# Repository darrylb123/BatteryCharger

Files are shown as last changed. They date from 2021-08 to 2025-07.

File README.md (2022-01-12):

# BatteryCharger
Multiplexed Battery Charger for maintaining up to 7 batteries from one charger, an 8th battery can be connected and charged but not maintained.

Based on the ESP12F\_Relay\_X8\_V1.1 integrated ESP8266 8 relay board.
A connected charger cycles through each battery in turn. The analog input monitors the battery terminal voltage of the battery. 

The charger is disconnected to measure the actual battery terminal volts by the No 8 relay therefore each module can manage 7 batteries. 

The board operates as an AP with captive portal or connects to a local network. Connecting to the AP with a mobile phone displays the normal captive portal login page, in this case it simply displays the battery status.
Use the Expressif Android app to connect the wifi the local network.

Electricals drawings by Qelectrotech.

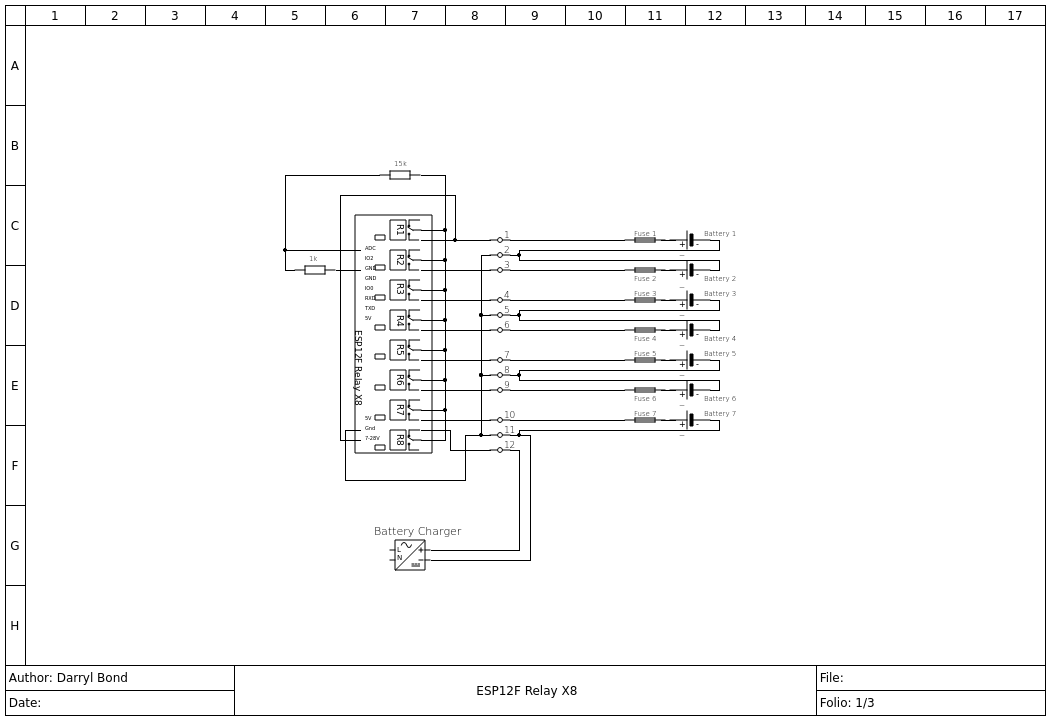
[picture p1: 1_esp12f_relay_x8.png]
7 Battery Wiring Diagram
 

## Construction
	- Connect the 1k resistor  between the ADC and GND and the 15k resistor between ADC and one of the COM terminals. (see Photograph)
	- Connect the 7-28V terminal to the NO8 relay
	- Connect the GND to the battery ground on the external terminal strip.
	- Follow the schematic to jumper between the module terminal strip and the external terminal strip.

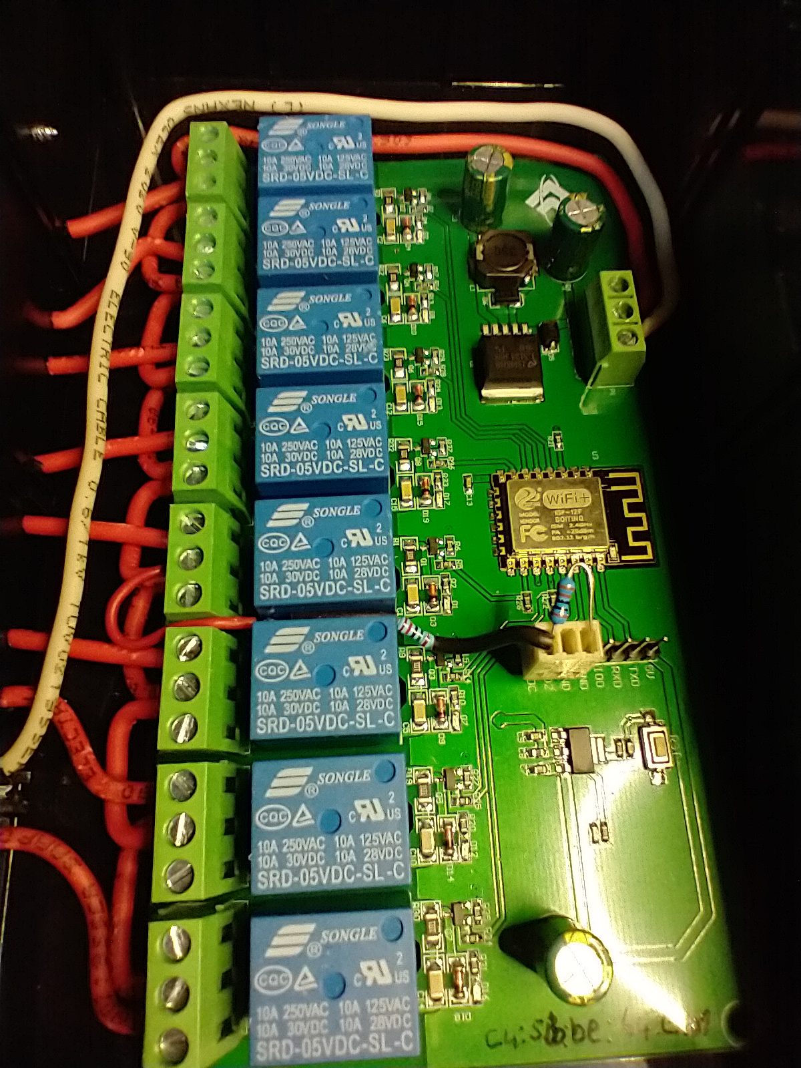
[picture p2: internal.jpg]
Relay module wiring

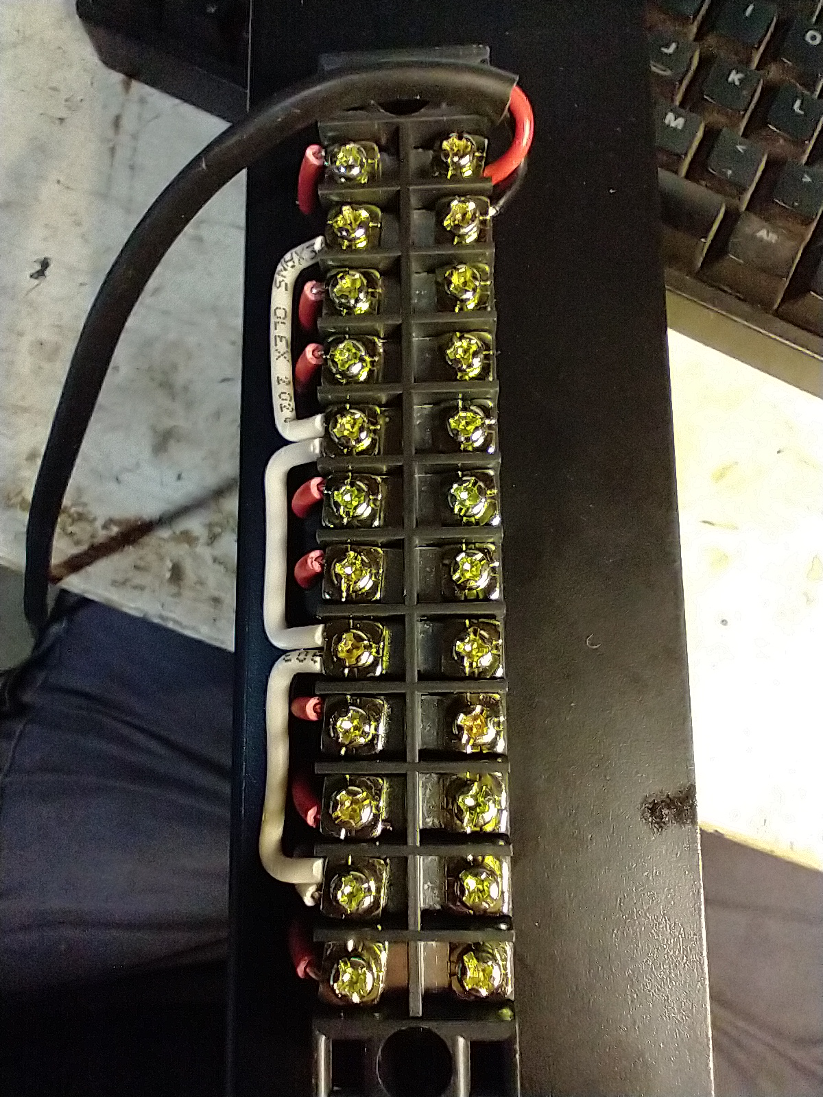
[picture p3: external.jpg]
External strip wiring


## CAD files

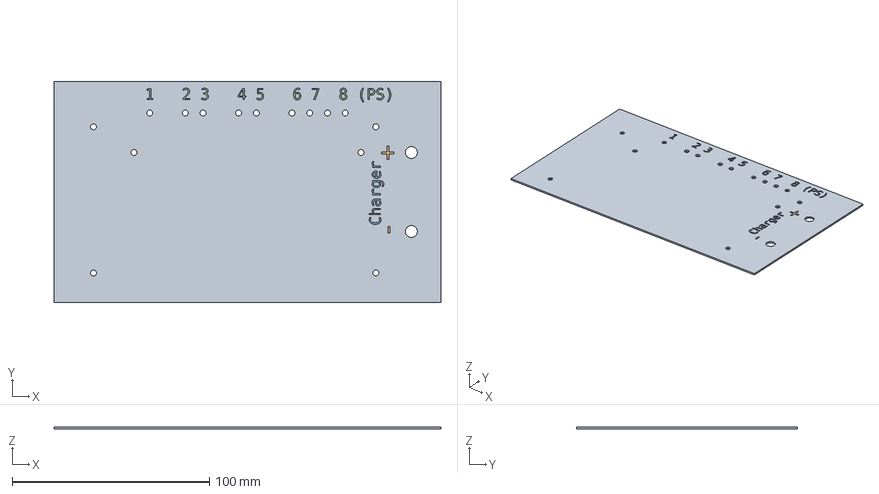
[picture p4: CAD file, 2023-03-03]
BatteryChargerLid.FCStd
196.0 x 112.0 x 1.00 mm
+-String
ChargerString
ShapeString002

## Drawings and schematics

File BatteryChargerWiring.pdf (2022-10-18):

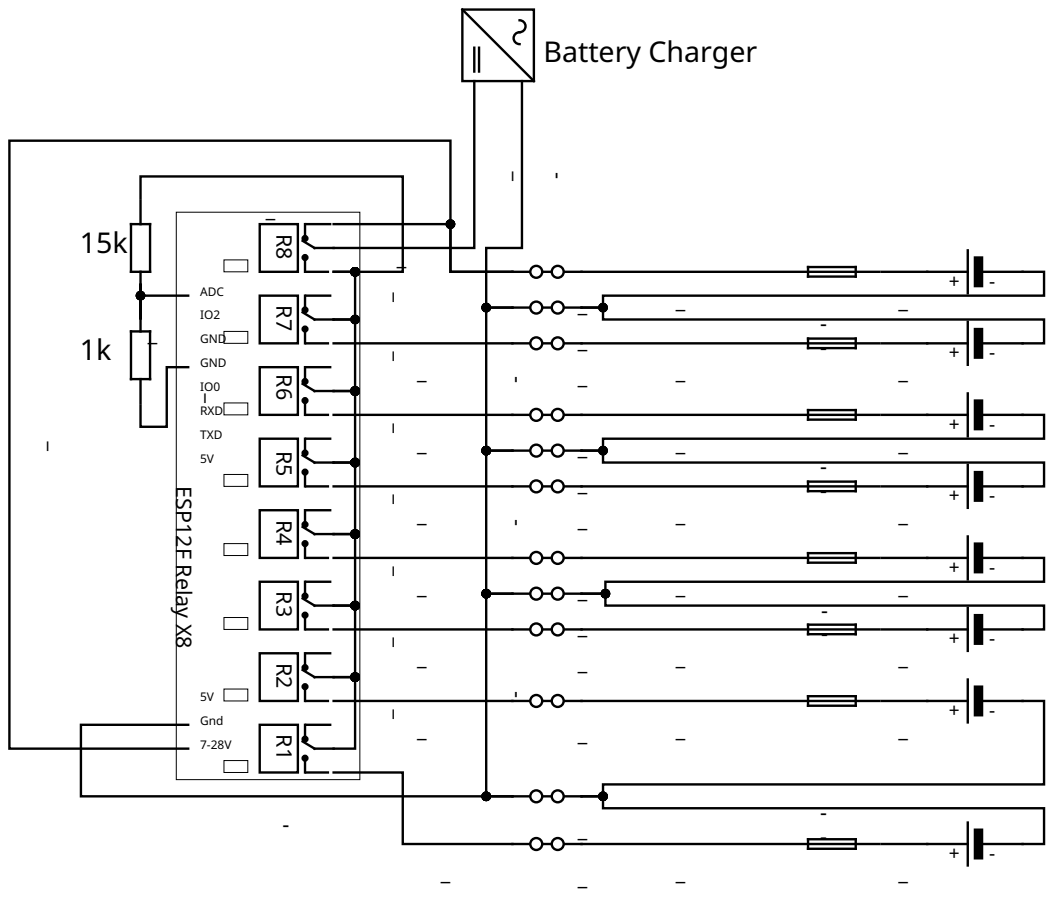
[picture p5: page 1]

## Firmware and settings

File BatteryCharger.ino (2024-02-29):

/* Battery Charger Multiplexer using ESP8266 or ESP32*/
/*
Copyright (C) 2021  Darryl Bond
This program is free software; you can redistribute it and/or modify
it under the terms of the GNU General Public License as published by
the Free Software Foundation; either version 2 of the License, or
(at your option) any later version.
This program is distributed in the hope that it will be useful,
but WITHOUT ANY WARRANTY; without even the implied warranty of
MERCHANTABILITY or FITNESS FOR A PARTICULAR PURPOSE.  See the
GNU General Public License for more details.
You should have received a copy of the GNU General Public License along
with this program; if not, write to the Free Software Foundation, Inc.,
51 Franklin Street, Fifth Floor, Boston, MA 02110-1301 USA.
*/
#define STATION 1
// #define SOFTAP 1
#define VER2 1
#define DEBUG 0
#define NEEDMQTT 1
#include <stdio.h>
#include <Ticker.h>

#if defined(VER2)
#define ENERG LOW
#define DEENERG HIGH
#else
#define ENERG HIGH
#define DEENERG LOW
#endif


#include "DNSServer.h"                  // Patched lib
// Capture DNS requests on port 53 in SoftAP Mode
IPAddress         apIP(10, 10, 10, 1);    // Private network for server
DNSServer         dnsServer;              // Create the DNS object



#include <ESP8266WiFi.h>
#include <ESP8266WiFiType.h>

const int RELAYS = 7;

struct Config {
  String mqttBroker;
  int mqttPort;
  String mqttUser;
  String mqttPasswd;
  String mqttTopic;
  float calConst;
  String labelTXT[RELAYS];
};

Config config;    // <- global configuration object

// An array of charging time indexed by the measured voltage. Allows a flat battery to be charged longer and a fully charged battery to be charged for a short time
// Volts                     0, 1,  2,  3,  4,  5,  6,  7,  8,    9,    10,   11,   12, 13, 14, 15, 16
const int CHARGEMINUTES[] = {1, 1,  1,  1,  60,  30, 10, 1, 240,  240,  240,  100,  10, 1,  1,  1,  1};
const float fullyCharged[] = {6.2,11.9};
const byte        DNS_PORT = 53;
String inputString;
int stringComplete;
int needDNS;

Ticker minutes;








#if defined(VER2) 
const int gpioPin[] = { 16, 14, 12, 13, 15, 0, 4 };
const int chargeEnable =  5 ;
const int bankPin[] = { 3, 3, 3, 3, 3, 3, 3 }; // Relay bank enable pin
const float CALIBRATION = 0.0157521; //15k/1k ohm resistors. Analog in is 0-1V (12/782 measured)
#else
const int gpioPin[] = { 16, 5, 4, 14 ,12, 13, 0};
const int chargeEnable = 2;
// const int gpioPin[] = { 16, 5, 4, 0, 2, 14, 12 };
// const int chargeEnable = 13;
const int bankPin[] = { 15, 15, 15, 15, 15, 15, 15 }; // Relay bank enable pin
const float CALIBRATION = 0.014273256; // 8.2/2.2 ohm resistor divider (3.313 / .694V = 234 of 1024 )
#endif

const int sensorPin = A0;





const int SCAN = 1000; // Delay in ms between each battery when scanning 
const int TESTCYCLE = 15; // Cycle time for testing batteries
char sapString[30]; // SSID and mqtt name unique by reading chip ID
float batVolts[RELAYS];
int batteryCharged[RELAYS];
int batteryConnected[RELAYS];
int allCharged = 0;
int currentCharger = 0 ;
int sensorValue = 0;
int firstBoot = 1;
int lastMinutes, lastHour, lastDay;
int runMinutes = 0;
int runHours = 0;
int runDays = 0;
char *responseHTML;
int forceCharge = 0;
int forceScan = 0;



void setup() {
  Serial.begin(115200);
  // Start Minute Ticker
  // Ticker is where all the action happens
  minutes.attach(60, eachMinute);

  wifiStartup();
  configSetup();
  initialiseWebUI();
  

  
  pinMode(chargeEnable, INPUT);
  Serial.print("chargeEnable Pin reads: ");
  Serial.println(digitalRead(chargeEnable));
  // Set direction of IO
  pinMode(chargeEnable, OUTPUT);
  for (int i = 0; i < RELAYS; i++) {
    pinMode(gpioPin[i], OUTPUT);
    pinMode(bankPin[i], OUTPUT);
    digitalWrite(gpioPin[i], ENERG);
    digitalWrite(bankPin[i], DEENERG); // The bank pin supplies 3.3V for the optocouplers supply. DEENERG disables the particular bank
  }
  currentCharger = 0;
  forceCharge = 0;
  forceScan = 0;
  scanAll(); // Scan all Batteries on boot
  batteriesCharged(); // See if they are allCharged
  
 
  if (!allCharged) 
    pickBattery(currentCharger); //Start with the first battery
  lastMinutes = runMinutes;
  lastDay = runDays;
  firstBoot = 1;
  
  delay(1000);
}


// Function Runs from the minute ticker
// Does all the work with deciding when to change relays
void eachMinute (){
  // Routine runs every minute
  logbat();
  runMinutes++;
  if (runMinutes < lastMinutes){
    lastMinutes = runMinutes;
    lastDay = runDays;
  }
  if ( ! (runMinutes % TESTCYCLE) ) {
    runHours++;
  }
  if ( ! (runMinutes % 1440) ) {
    runDays++;
  }
  // Check if the charge time on current has expired and increment battery number
  // See if we have rolled over, delayed enough or current battery has < 1.2V
  // if all batteries are charged, pickBattery will set the lastDay 1 in front so that it waits until then to attempt charging again
  if (runMinutes >= (lastMinutes + CHARGEMINUTES[(int)batVolts[currentCharger]]) ) {
    lastMinutes = runMinutes;
    lastDay = runDays;
    currentCharger++;
  }
  
  if (allCharged)
    currentCharger = 0;

  if (currentCharger >= RELAYS ) { // At the end of a cycle check all the batteries to see if any need charging again
    currentCharger = 0;
    // Reset force Charge flag
    forceCharge = 0;
    scanAll(); 
  }
  // Check if all batteries are charged. pickBattery wont charge any if all charged
  pickBattery(currentCharger);
}

void scanAll(){
  int j;
  // scan all the batteries for voltage
  // Disable the charger to read actual battery volts
  Serial.println("Scanning");
  // Initialise all pins to off
  
  // Set all Charged to off to allow reading voltages
  allCharged = 0;
  currentCharger = 0;
  //Energise the charger relay
  digitalWrite(chargeEnable, ENERG);
  for (int i = 0; i < RELAYS; i++) {
    for (int i = 0; i < RELAYS; i++) {
      digitalWrite(gpioPin[i], ENERG);
      digitalWrite(bankPin[i], DEENERG);
    }
    j = millis();
    while(millis() < (j+SCAN)){
      webLoop();
    }
    digitalWrite(bankPin[i], ENERG);
    delay(100); // Allow time to power the module
    digitalWrite(gpioPin[i], DEENERG);
    
    delay(100);
    j = millis();
    while(millis() < (j+500)){
      batteryState(i);
      webLoop();
    }
    
    Serial.print(" ");
    Serial.print(batVolts[i]);
    Serial.print(" ");
    Serial.print(batteryCharged[i]);
    Serial.print(batteryConnected[i]);
  }

  Serial.println(" ");
#if defined(NEEDMQTT)
  if (WiFi.status() == WL_CONNECTED) {
    publishData();
  }
#endif
  for (int i = 0; i < RELAYS; i++) {
    digitalWrite(gpioPin[i], ENERG);
    
    digitalWrite(bankPin[i], DEENERG);
  }
  batteriesCharged();

}

// Check if all the batteries are charged
int batteriesCharged(){
  allCharged = 1;
  for (int i = 0; i < RELAYS; i++) {
    if (batteryConnected[i] && !batteryCharged[i]) {
      allCharged = 0;
    }
  }
  if (forceCharge) {
    allCharged = 0;
  }
  return(allCharged);
}
// Change the relays, either to the next relay or scan all for voltages
void pickBattery(int num) {
  for (int i = 0; i < RELAYS; i++) {
    digitalWrite(gpioPin[i], ENERG);
    digitalWrite(bankPin[i], DEENERG);
  }
  if (num < RELAYS && !batteriesCharged()) { // if the number is the same as NUMBER OF RELAYS then check all
    digitalWrite(gpioPin[num], DEENERG);
    digitalWrite(bankPin[num], ENERG);
  } 
}

int batteryState(int batnum) { 
  if (batnum >= RELAYS) {
    Serial.println("Error: Past End of RELAYS Array");
    return(0);
  }
  // if(allCharged) return(0);
  
  int rel = digitalRead(gpioPin[batnum]);
  int bank = digitalRead(bankPin[batnum]);
  int enabled = digitalRead(chargeEnable);

  if ( enabled == DEENERG ) {
    Serial.println("Charger is enabled, no point reading voltage");
    return(0); 
  }
  if ( rel == ENERG || bank == DEENERG ) {
    char err[50];
    sprintf(err,"Error Relay %d not zero %d or bank one %d",batnum + 1, rel, bank);
    Serial.println(err);
    return(0);
  }
  
  batVolts[batnum] = analogRead(sensorPin) * config.calConst;
  
  if (batVolts[batnum] > 4.0 && batVolts[batnum] < 15.2) { // Some chargers have 16V or so open circuit
    batteryConnected[batnum] = 1;
    if ((batVolts[batnum] < 8.0) && (batVolts[batnum] > fullyCharged[0] )) // 6V Battery
      batteryCharged[batnum] = 1;
    else if (batVolts[batnum] > fullyCharged[1]) { //12V Battery
      batteryCharged[batnum] = 1;
    } else {
        batteryCharged[batnum] = 0;
    }
  } else {
      batteryConnected[batnum] = 0;
      batteryCharged[batnum] = 0;
  }
  return(batteryCharged[batnum]);
}


void loop() {
  wifiLoop();
  webLoop();
  if (forceScan){
    scanAll();
    forceScan = 0;
  }
  // Read the battery voltage each hour if fully charged
  if ((runHours > lastHour) && batteriesCharged()) {
    scanAll();
    lastHour = runHours;
  }
  // If Batteries need to be charged - Energise the Charger enable relay
  if (!batteriesCharged()){
    digitalWrite(chargeEnable, DEENERG);
  } else {
    digitalWrite(chargeEnable, ENERG);
  }
}

void logbat () {
  int t = analogRead(sensorPin);
  String bat = "Selected battery ";
  String theTime = "Run Time: ";
  theTime = theTime + " " + runMinutes + " minutes " + runHours + " hours " + runDays + " days ";
  int num = currentCharger ;
  bat = theTime + " " + bat + num + " " + t + " " + String(t * config.calConst, 2);
  if (allCharged)
    bat = bat + " All Charged";
  Serial.println(bat);
}

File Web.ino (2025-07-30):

#include <ESP8266WebServer.h>
#include <WiFiClient.h>
#include <ESP8266WiFi.h>
#include <ESP8266mDNS.h>
#include <FS.h>
#include <LittleFS.h>

#define MYFS LittleFS
#define FORMAT_LITTLEFS_IF_FAILED 


ESP8266WebServer  webServer(80);          // HTTP server



const char* serverIndex = 
"<script src='https://ajax.googleapis.com/ajax/libs/jquery/3.2.1/jquery.min.js'></script>"
"<form method='POST' action='#' enctype='multipart/form-data' id='upload_form'>"
   "<input type='file' name='update'>"
        "<input type='submit' value='Update'> (or Reboot)"
    "</form>"
 "<div id='prg'>progress: 0%</div>"
 "<script>"
  "$('form').submit(function(e){"
  "e.preventDefault();"
  "var form = $('#upload_form')[0];"
  "var data = new FormData(form);"
  " $.ajax({"
  "url: '/update',"
  "type: 'POST',"
  "data: data,"
  "contentType: false,"
  "processData:false,"
  "xhr: function() {"
  "var xhr = new window.XMLHttpRequest();"
  "xhr.upload.addEventListener('progress', function(evt) {"
  "if (evt.lengthComputable) {"
  "var per = evt.loaded / evt.total;"
  "$('#prg').html('progress: ' + Math.round(per*100) + '%');"
  "}"
  "}, false);"
  "return xhr;"
  "},"
  "success:function(d, s) {"
  "console.log('success!')" 
 "},"
 "error: function (a, b, c) {"
 "}"
 "});"
 "});"
 "</script>";
 
// Various functions to build the web pages
void initialiseWebUI(){
  // Allocate web page memory
  responseHTML = (char *)malloc(20000);
  webServer.on("/", handlePage);
  webServer.on("/postform/", handleForm);
  webServer.on("/rmfiles", rmfiles);
  webServer.on("/editlabels", formPage);
  webServer.on("/forcecharge", forceChargeCycle);
  webServer.on("/forcescan", forceScanCycle);
  webServer.on("/connectAP", connectAP);
  webServer.on("/serverIndex", HTTP_GET, []() {
  webServer.sendHeader("Connection", "close");
  webServer.send(200, "text/html", serverIndex);

  webServer.on("/update", HTTP_POST, []() {
      webServer.sendHeader("Connection", "close");
      webServer.send(200, "text/plain", (Update.hasError()) ? "FAIL" : "OK");
      ESP.restart();
    }, []() {
      HTTPUpload& upload = webServer.upload();
      if (upload.status == UPLOAD_FILE_START) {
        Serial.setDebugOutput(true);
        WiFiUDP::stopAll();
        Serial.printf("Update: %s\n", upload.filename.c_str());
        uint32_t maxSketchSpace = (ESP.getFreeSketchSpace() - 0x1000) & 0xFFFFF000;
        if (!Update.begin(maxSketchSpace)) { //start with max available size
          Update.printError(Serial);
        }
      } else if (upload.status == UPLOAD_FILE_WRITE) {
        if (Update.write(upload.buf, upload.currentSize) != upload.currentSize) {
          Update.printError(Serial);
        }
      } else if (upload.status == UPLOAD_FILE_END) {
        if (Update.end(true)) { //true to set the size to the current progress
          Serial.printf("Update Success: %u\nRebooting...\n", upload.totalSize);
        } else {
          Update.printError(Serial);
        }
        Serial.setDebugOutput(false);
      }
      yield();
    });

  });
  webServer.onNotFound(handlePage);
  webServer.begin();

}
// Label form page
void formPage () {
  char tempstr[1024];

  strcpy(responseHTML, "<!DOCTYPE html><html><head>\
                      <title>Battery Charger</title></head><body>\
                      <style>\
                      table {\
  border-collapse: collapse;\
  width: 100%;\
  font-size: 30px;\
}\
\
table, th, td {\
  border: 1px solid black;\
}\
</style>\
<H1> Battery Charger Configuration</H1>\
<form method=\"post\" enctype=\"application/x-www-form-urlencoded\" action=\"/postform/\">");


  strcat(responseHTML, "<TABLE><TR><TH>Configuration</TH><TH>Setting</TH>\n");

  for (int i = 0; i < RELAYS; i++) {
    sprintf(tempstr, "<TR><TD>Battery %d Label </TD><TD><input type=\"text\" name=\"%d\" value=\"%s\"> </TD><TR>\n",
              i + 1,i + 1,config.labelTXT[i].c_str());
    strcat(responseHTML, tempstr);
  }


  sprintf(tempstr, "<TR><TD>Calibration Constant(%5f):</TD><TD> Enter Displayed Voltage: <input type=\"text\" name=\"Displayed\" value=\"\"> Enter Expected Voltage: <input type=\"text\" name=\"Expected\" value=\"\"></TD><TR>\n",config.calConst);
  strcat(responseHTML, tempstr);

#if defined(NEEDMQTT)
  sprintf(tempstr, "<TR><TD>MQTT Broker Hostname or IP Address (eg public.mqtthq.com):</TD><TD> <input type=\"text\" name=\"mqttBroker\" value=\"%s\"></TD><TR>\n\n",config.mqttBroker.c_str());
  strcat(responseHTML, tempstr);
  sprintf(tempstr, "<TR><TD>MQTT Broker Port : </TD><TD><input type=\"text\" name=\"mqttPort\" value=\"%d\"></TD><TR>\n\n",config.mqttPort);
  strcat(responseHTML, tempstr);
  sprintf(tempstr, "<TR><TD>MQTT Broker User :</TD><TD> <input type=\"text\" name=\"mqttUser\" value=\"%s\"></TD><TR>\n\n",config.mqttUser.c_str());
  strcat(responseHTML, tempstr);
  sprintf(tempstr, "<TR><TD>MQTT Broker Password :</TD><TD> <input type=\"text\" name=\"mqttPasswd\" value=\"%s\"></TD><TR>\n\n",config.mqttPasswd.c_str());
  strcat(responseHTML, tempstr);
  sprintf(tempstr, "<TR><TD>MQTT Topic :</TD><TD> <input type=\"text\" name=\"mqttTopic\" value=\"%s\"></TD><TR>\n\n",config.mqttTopic.c_str());
  strcat(responseHTML, tempstr);

#endif
  strcat(responseHTML, "</TABLE>");
  strcat(responseHTML, "<input type=\"submit\" value=\"Submit\"></form>");
  strcat(responseHTML, "The Calibration Constant is the factor the Analog to Digital converter value is multiplied with to produce the displayed battery voltage.\
  This can be wrong due to variations in the resistors used on each board.\
  To correct the calibration, note the displayed battery volts on a battery and the measured voltage on the same \
  battery using a voltmeter and enter into the fields above.<br>\n");
  strcat(responseHTML, "<A href=\"/\">Return to Battery Display</A> </body></html>\n");
  if (DEBUG)
    Serial.print(responseHTML);
  delay(100);// Serial.print(responseHTML);
  webServer.send(200, "text/html", responseHTML);

}
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

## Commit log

2020-08-23 Using variable charge times based on the current charge volts
2020-08-24 Added support for ESP32 using #defines
2020-08-24 Added wiring diagram and documentation
2020-09-02 Fixed orientation of the charge load relay
2020-09-03 Fixed ESP32 support
2020-09-07 Changed to minute ticks from millis()
2020-09-10 Charging flags
2020-09-17 Added the ability to delay when all batteries are charged
2020-09-19 Added hourly scan which fully charged
2020-09-30 Better analog polling when not charging
2020-10-07 Additions to try to resolve connection failure and reboots on wifi
    [BatteryCharger.ino]
2020-10-08 Added a 2 second delay in SoftAP configuration mode to fix crashes when connecting.
    [BatteryCharger.ino]
2020-10-13 Added ESP Smart config for Wifi
    Added the ability to bus multiple relay modules with a gpio for each module to power the optocouplers for the bus.
2020-10-18 Sr\tring causing webserver to crash
    [BatteryCharger.ino]
2020-10-19 Changed from String object in the web page to char strings in the attempt to stop crashing after a while.
    [BatteryCharger.ino]
2020-10-19 Fix mistake on web page
    [BatteryCharger.ino]
2020-11-26 Fixed first start logic bug
    [BatteryCharger.ino]
2020-12-08 Updated the schematic
2020-12-13 Tested support for 16 relays using bussed bank select
2021-01-28 Fixed compiler error due to hidden characters in file
    [BatteryCharger.ino]
2021-02-08 Print hostname at startup
2021-02-11 Compiles on ESP8266 and ESP32 Needs some work around a Label form rather than use the main page that refreshes.
2021-02-17 Extra test for battery voltage
2021-02-23 iUpdate battery state all the time
2021-02-24 Refactored the core to simplifiy the logic. Split the charger function into Wifi and Web server files
2021-02-25 Added better wifi error handling and logic around charged checking
    [BatteryCharger.ino, Wifi.ino]
2021-02-25 Chasing a race on battery 1
2021-03-01 Added tests to make sure a relay is energised before measuring the battery volts. Gets around a strnage race.
2021-03-16 Initialise all relays to zero before scanning
2021-03-27 Relay 8 in each bank now disconnects the battery charger for the voltage scan
2021-03-27 Fixed some logic. Batteries are checked every 15min when charged and at the end of a charge cycle
    [BatteryCharger.ino]
2021-04-19 14 Battery Charger Schematic QElectrotech
2021-04-19 No longer using dia to edit schematic
2021-04-22 Added 7 way (single relay module) charger and exported PNG
2021-04-22 Added the new drawings and adjusted the README to reflect the new charger properties
2021-08-12 Added support for all in one module VER2 (ESP8266 with 8 relays)
2021-08-12 Fixed logic around reading voltage. Should be right for either version.
    [BatteryCharger.ino]
2021-08-20 Documentation now only reflects the ESP12F Relay X8 module
2021-08-24 Added fuses and tidied text sizes
2021-10-01 Disconnects the battery charger once per scan rather thabn each battery. Added a software reset link
    [BatteryCharger.ino, Web.ino]
2021-10-01 Firmware update page also reboots
    [Web.ino]
2022-01-12 Modified to allow unmanaged battery to be connected to 8th relay
2022-01-17 Added force charge button
2022-01-17 Removed ESP32 code to remove the complexity. Changed the logic so that wifi defaults to AP mode unless it can connect. Use ESPTouch app to connect.
2022-04-17 Fixed the V1 gpio pins
    [BatteryCharger.ino]
2022-05-13 Added ability to change the calibration constant. 1% resistors and all that. Edit field in the Label change screen
2022-05-13 Wiring Diagram
2022-07-29 Fixed Wiring
2022-10-18 Fix drawing, Relays numbering incorrect
2023-03-03 Added mqtt publish of voltage. Bug in mqtt server form handling.
    [BatteryCharger.ino, Web.ino, Wifi.ino]
2023-03-03 Modified to use JSON configuration and mqtt
    [BatteryChargerLid.FCStd]
2023-03-04 Added simplified method of fixing the calibration constant by entering the displayed voltage and the expected voltage.
    [Web.ino]
2024-02-25 Handle 6V batteries correctly
    [BatteryCharger.ino, mqtt.ino]
2024-02-27 Fixed a little bug
    [BatteryCharger.ino]
2024-02-29 Tidied up mqtt error handling
    [BatteryCharger.ino, Web.ino, mqtt.ino]
2024-03-01 iALlow use of stored fixed ssid/pw
    [Wifi.ino]
